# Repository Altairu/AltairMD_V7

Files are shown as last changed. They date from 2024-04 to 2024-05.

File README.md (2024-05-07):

# [**AltairMD_V7**](https://github.com/Altairu/AltairMD_V7)
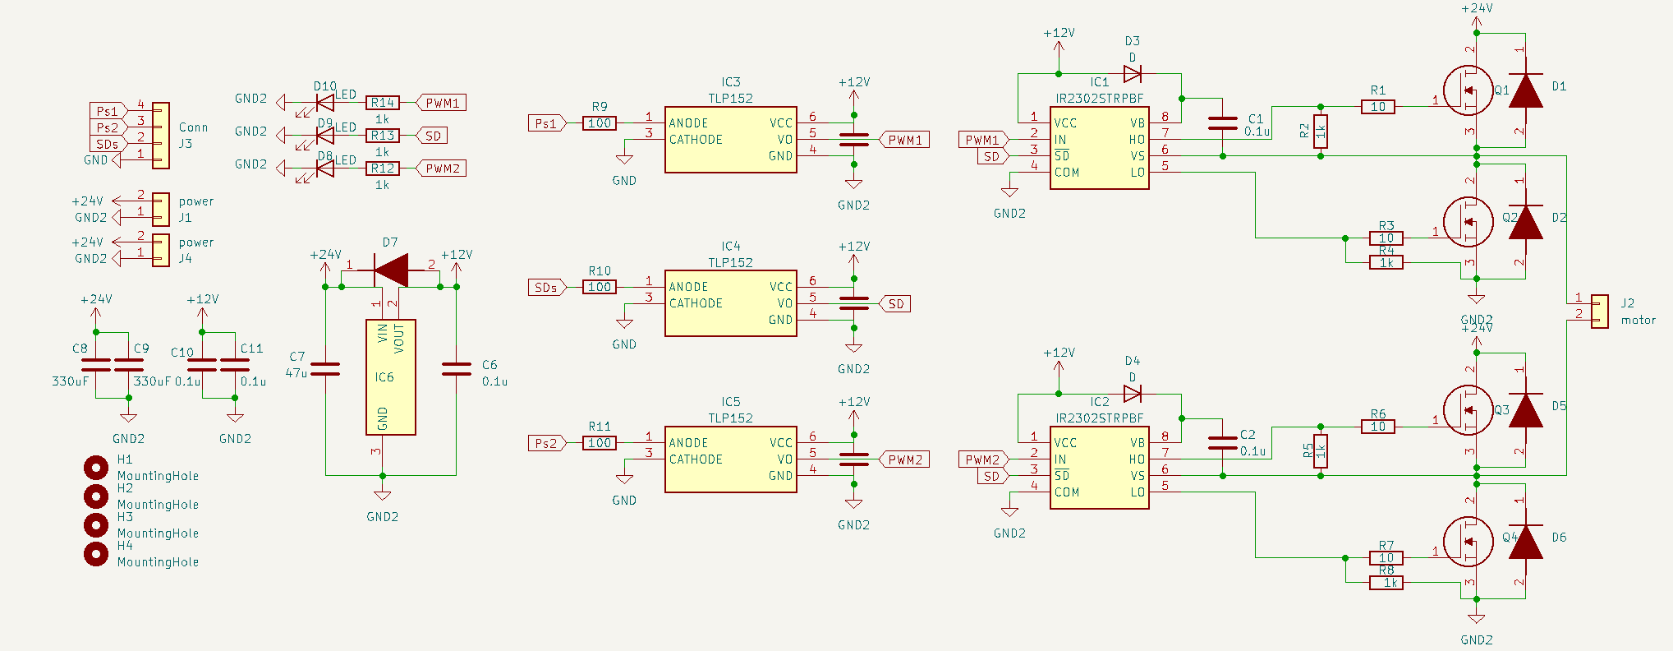
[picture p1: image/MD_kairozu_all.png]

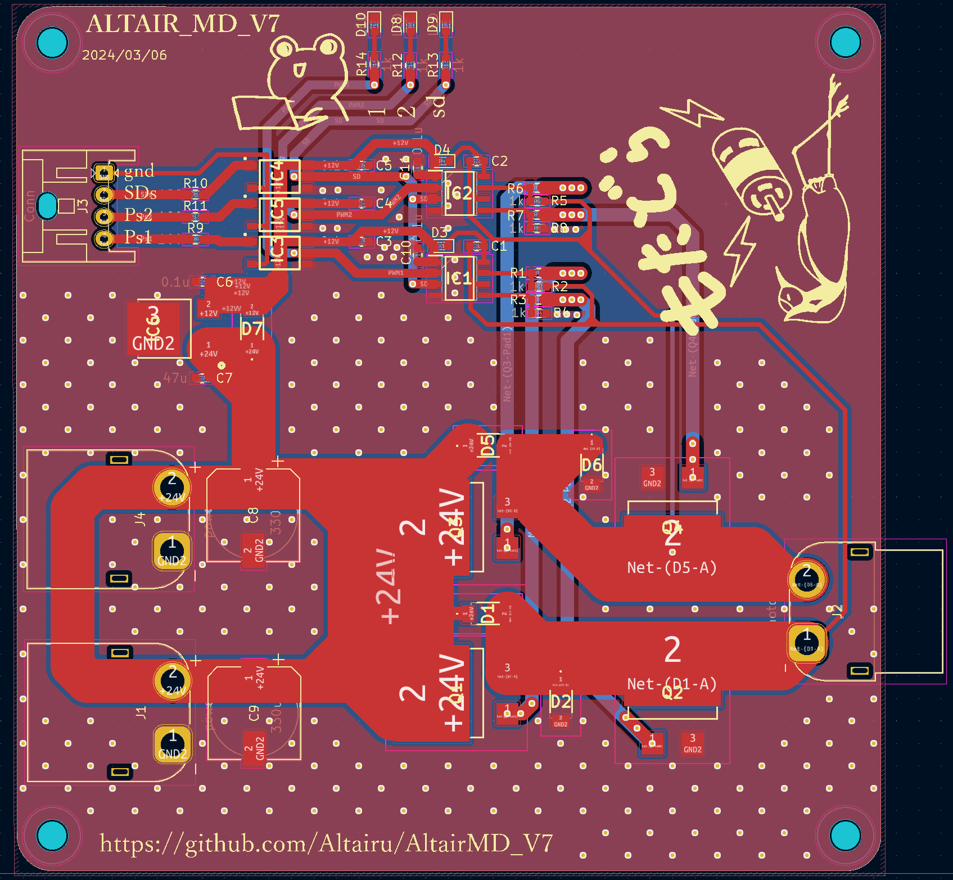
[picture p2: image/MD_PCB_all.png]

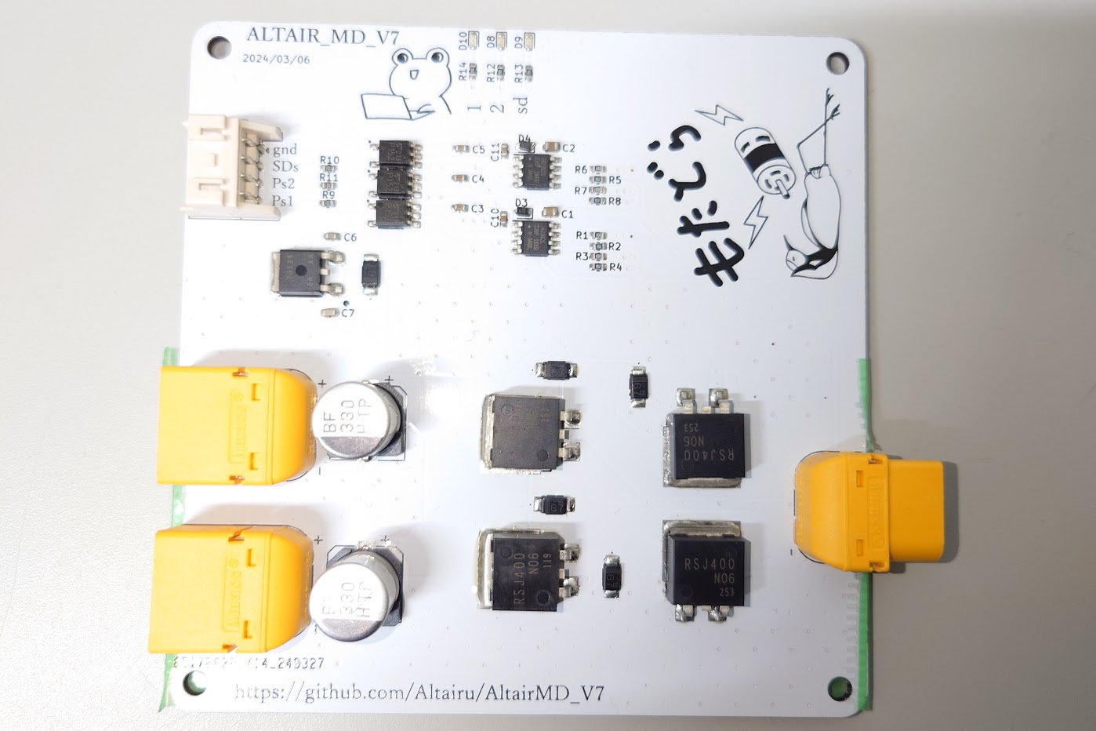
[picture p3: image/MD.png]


https://github.com/Altairu/AltairMD_V7
---
# **仕様**
* 30V~10V(フォトカプラを変更すると10V以下も可)
* 最大40A 

|SDs|Ps1|Ps2|出力|
|:----:|:----:|:----:|:----:|
|HIGH|LOW	|LOW	|停止|
|HIGH|LOW	|HIGH	|逆転|
|HIGH|HIGH	|LOW	|正転|
|HIGH|HIGH	|HIGH	|`ブレーキ`（非推奨）|
|LOW|X	|X	|0|

## **三端子レギュレーター** 
### **[NJM7812SDL1]()**
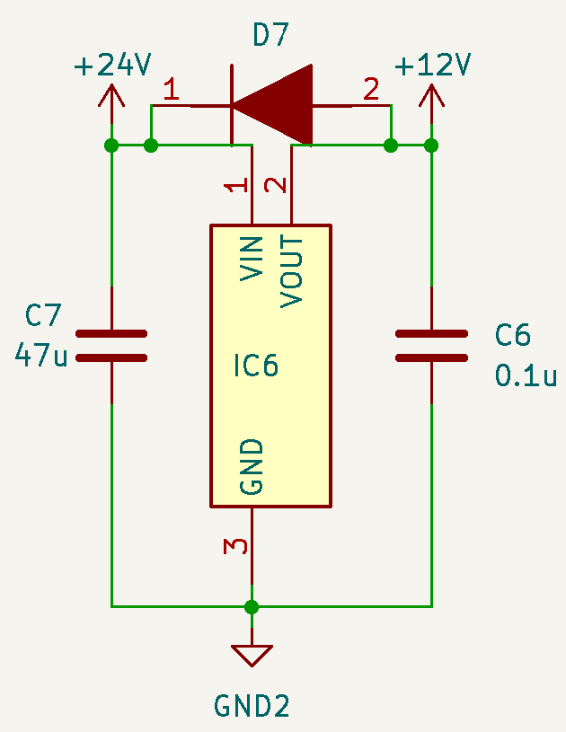
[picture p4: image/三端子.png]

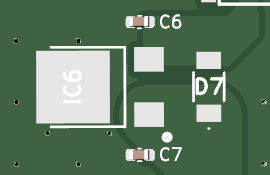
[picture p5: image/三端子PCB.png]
 

* **12Vに降圧**
* **端子が3つ(入力・グラウンド・出力）**
* **三端子レギュレータは落とした分の電圧をすべて`熱`として消費**
* **ダイオード**
レギュレータに逆電流が流れるのを防止
* **コンデンサ**
コンデンサは入力側と出力側に0.1～10[uF]程度入れるのが一般的

## **フォトカプラ**
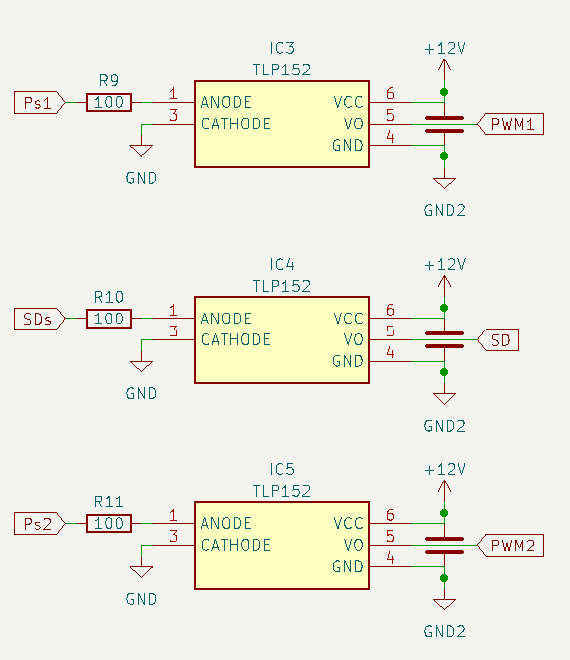
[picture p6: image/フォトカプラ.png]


### [TLP152](https://akizukidenshi.com/catalog/g/g110824/)
* 取り付け様式:	SMD/SMT	
* パッケージ/ケース:SOIC-6
* 電源電圧min.：10V
* 電源電圧max.：30V
* 出力電流：2A
* 入力電流max.：20mA
* 上昇応答時間：95ns
* 下降応答時間：110ns

## **MOSFET**
### [**RSJ400N10**](https://www.rohm.co.jp/products/mosfets/small-signal/single-nch/rsj400n10-product)

Nch 100V 40A Power MOSFET

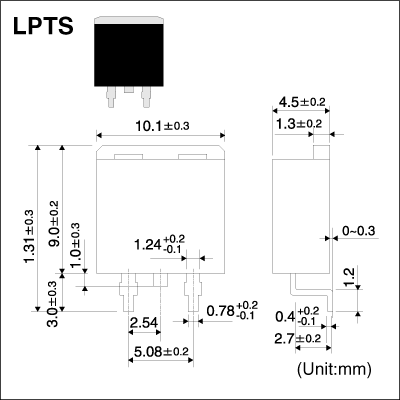
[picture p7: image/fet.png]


* 4V駆動タイプ
* Nチャンネル　パワーMOSFET
* 高速スイッチング
* 駆動回路が簡単
* 並列使用が容易

ゲート抵抗は10[Ω]で設定している

### **ハーフブリッジゲートドライバ**
### [**IR2302STRPBF**](https://akizukidenshi.com/catalog/g/g115656/)
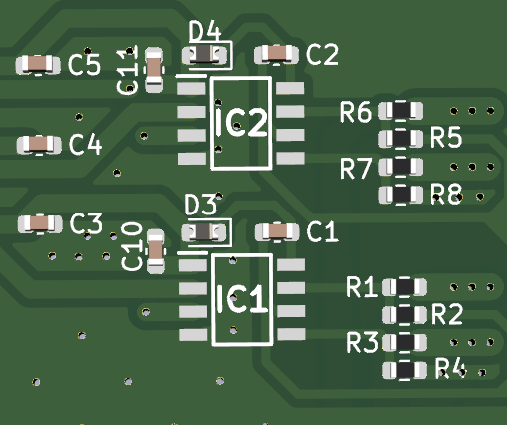
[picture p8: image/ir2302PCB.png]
 
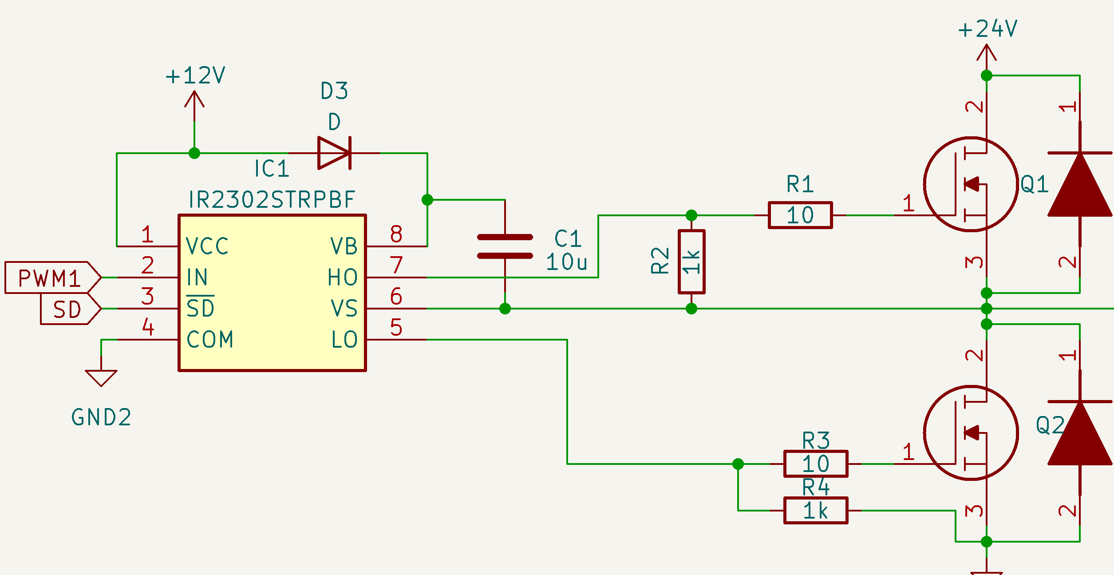
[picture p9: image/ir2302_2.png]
 
* IN端子
ハイサイドMOSFETをONにするか、ローサイドMOSFETをONにするかの切り替えを行う
Hが入力されるとハイサイド、Lが入力されるとローサイドがONとなる
**ハイサイドにNchMOSFETを使うためにブーストラップ回路を使用**
* ブートストラップコンデンサの容量は[10uF]
* ブートストラップダイオード
(ファストリカバリダイオード)
* `100％出力は不可`
ブートストラップ回路の制約で
コンデンサのチャージ時間が必要.

# Ｈブリッジ回路
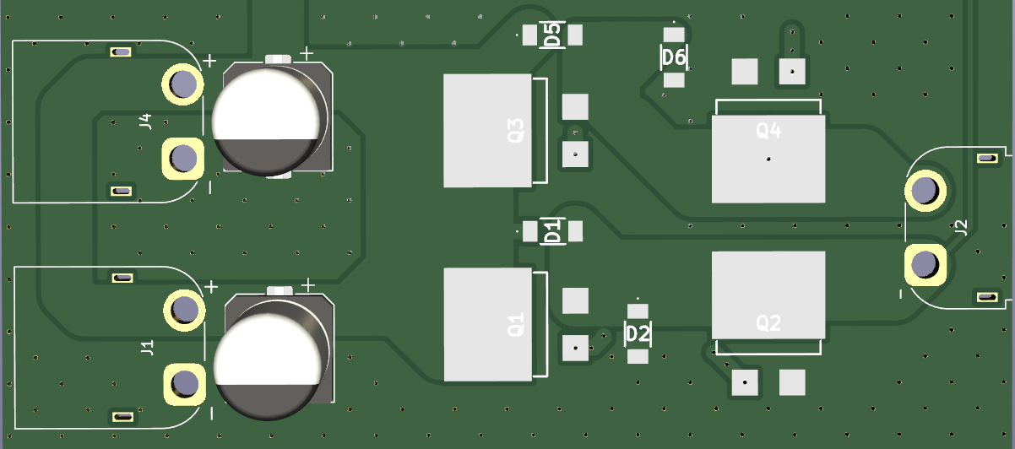
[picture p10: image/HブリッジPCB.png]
width:1000px
 

| Ps1 | Ps2 | Q1  | Q2  | Q3  | Q4  | 1 | 2 | 
| :----: | :----: | :----: | :----: | :----: | :----: | :----: | :----: |
| L | L | H | L | H | L | open | open | 
| L | H | H | H | L | L | L | H | 
| H | L | L | L | H | H | H | L | 
| H | H | H | H | H | H | L | L |

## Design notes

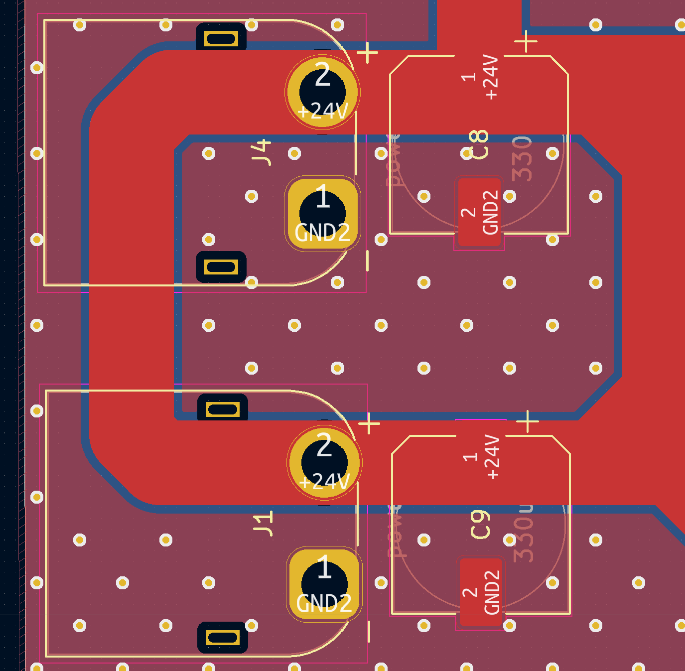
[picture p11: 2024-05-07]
image/バイパスコンPCB.png

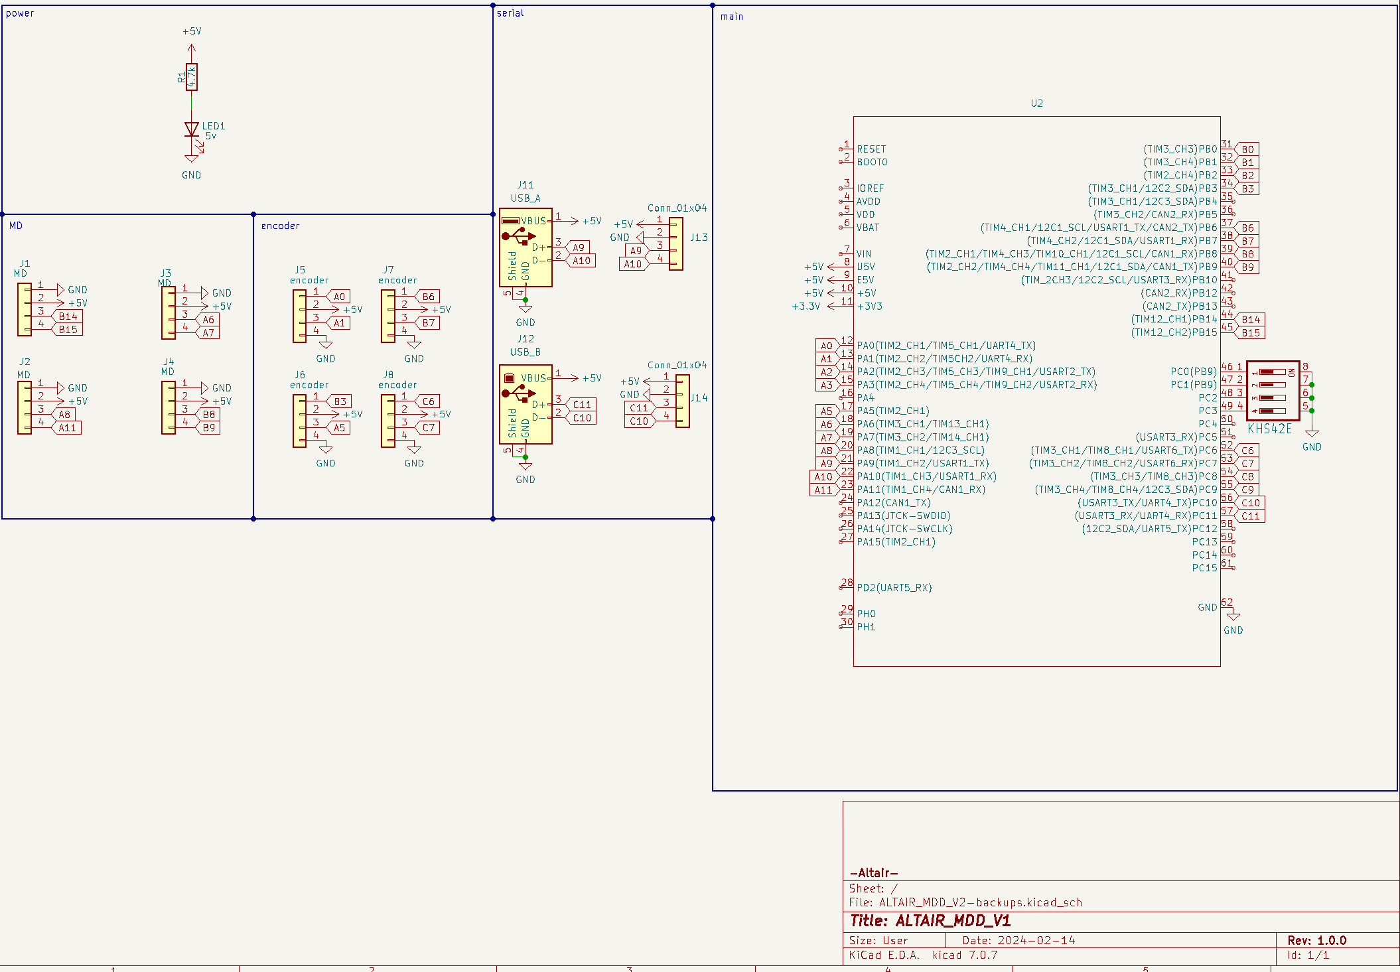
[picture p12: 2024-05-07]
image/MDD2.png

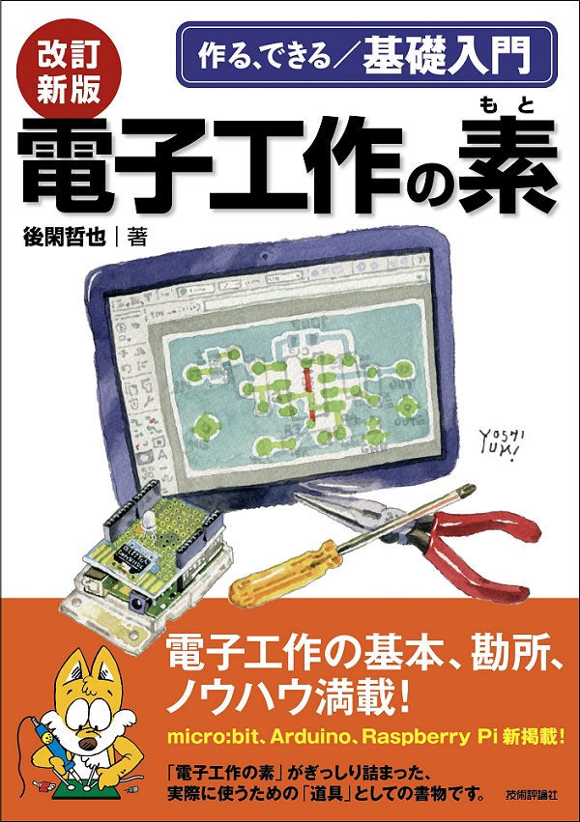
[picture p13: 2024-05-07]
image/kaironomoto.png

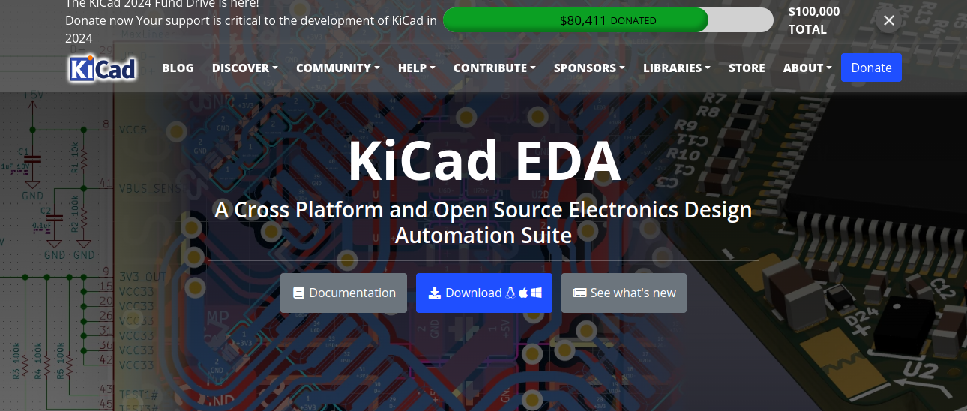
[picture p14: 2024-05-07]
image/kicad.png

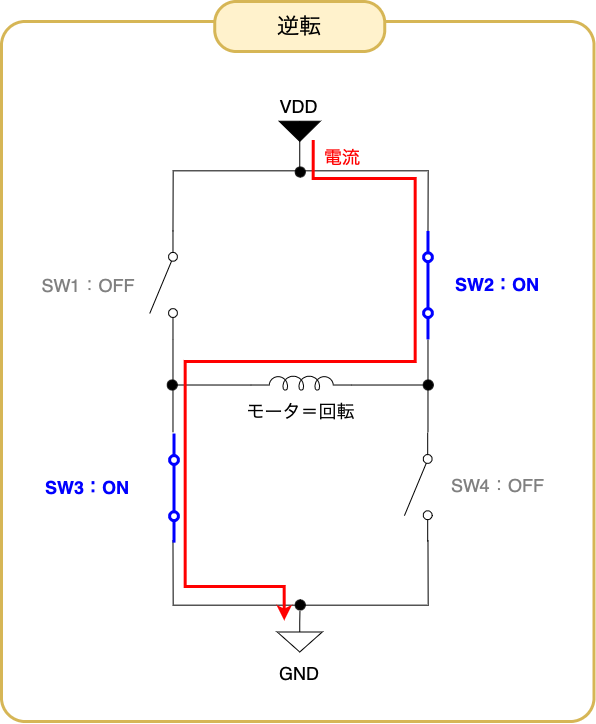
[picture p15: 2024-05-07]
image/1_files/165cf2e3f7085f0288b2cf0e68efcce5.png

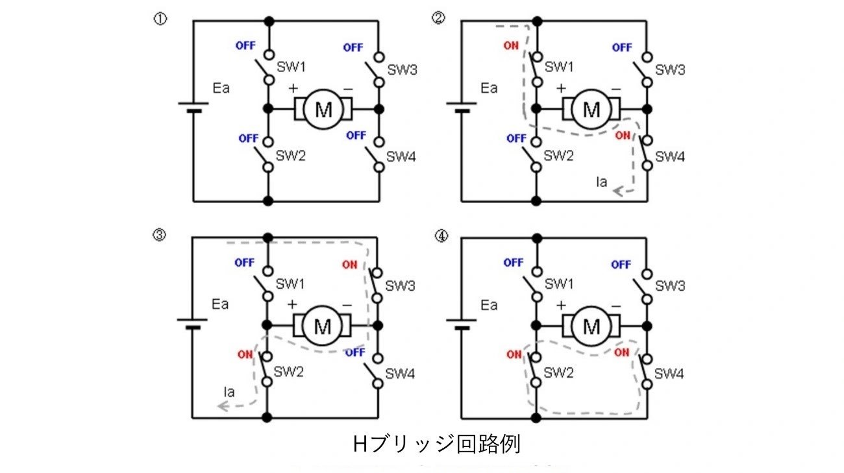
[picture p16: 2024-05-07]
image/Hブリッジ.png

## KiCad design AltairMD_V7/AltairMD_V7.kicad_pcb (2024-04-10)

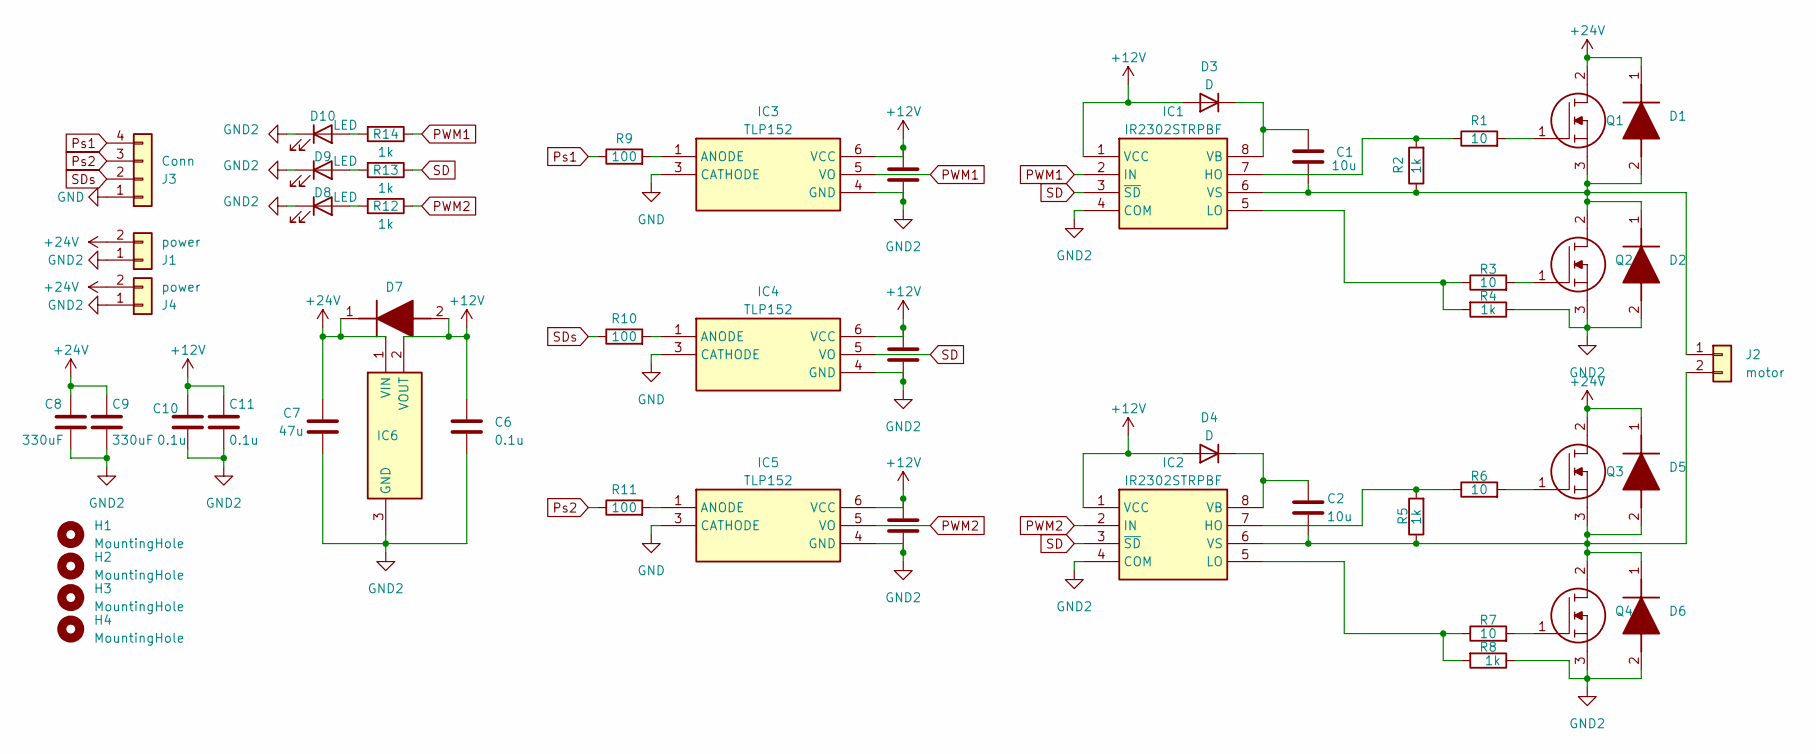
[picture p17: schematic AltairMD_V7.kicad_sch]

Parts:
C1, C2: 10u; C_0603_1608Metric
C3, C4, C5, C6, C10, C11: 0.1u; C_0603_1608Metric
C7: 47u; C_0603_1608Metric
C8, C9: 330uF; CP_Elec_10x10
D1, D2, D5, D6, D7: RF201LAM2STR; Manufacturer_Part_Number RF201LAM2STR
D3, D4: D; D_0603_1608Metric
D8, D9, D10: LED; LED_0603_1608Metric
H1, H2, H3, H4: MountingHole; MountingHole_3.2mm_M3
IC1, IC2: IR2302STRPBF; SOIC127P600X175-8N; Manufacturer_Part_Number IR2302STRPBF
IC3, IC4, IC5: TLP152; 11-4L1S_5-PIN-SOIC_; Manufacturer_Part_Number TLP152
IC6: NJM7800S-DL1; TO-252-3-L1; Manufacturer_Part_Number NJM7800S-DL1
J1, J4: power; AMASS_XT60PW-M_1x02_P7.20mm_Horizontal
J2: motor; AMASS_XT60PW-F_1x02_P7.20mm_Horizontal
J3: Conn; JST_XA_S04B-XASK-1_1x04_P2.50mm_Horizontal
Q1, Q2, Q3, Q4: RSJ400N06FRATL; R6024KNJTL; Manufacturer_Part_Number RSJ400N06FRATL
R1, R3, R6, R7: 10; R_0603_1608Metric
R2, R4, R5, R8, R12, R13, R14: 1k; R_0603_1608Metric
R9, R10, R11: 100; R_0603_1608Metric

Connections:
+12V: C3.1, C4.1, C5.1, C6.1, C10.1, C11.1, D3.2 (A), D4.2 (A), D7.2 (A), IC1.1 (VCC), IC2.1 (VCC), IC3.6 (VCC), IC4.6 (VCC), IC5.6 (VCC), IC6.2 (VOUT)
+24V: C7.1, C8.1, C9.1, D1.1 (K), D5.1 (K), D7.1 (K), IC6.1 (VIN), J1.2, J4.2, Q1.2, Q3.2
GND: IC3.3 (CATHODE), IC4.3 (CATHODE), IC5.3 (CATHODE), J3.1
GND2: C3.2, C4.2, C5.2, C6.2, C7.2, C8.2, C9.2, C10.2, C11.2, D2.2 (A), D6.2 (A), D8.1 (K), D9.1 (K), D10.1 (K), IC1.4 (COM), IC2.4 (COM), IC3.4 (GND), IC4.4 (GND), IC5.4 (GND), IC6.3 (GND), J1.1, J4.1, Q2.3, Q4.3, R4.1, R8.1
unnamed: C1.2, D1.2 (A), D2.1 (K), IC1.6 (VS), J2.1, Q1.3, Q2.2, R2.1
unnamed: C1.1, D3.1 (K), IC1.8 (VB)
unnamed: C2.1, D4.1 (K), IC2.8 (VB)
unnamed: C2.2, D5.2 (A), D6.1 (K), IC2.6 (VS), J2.2, Q3.3, Q4.2, R5.1
unnamed: D8.2 (A), R12.2
unnamed: D9.2 (A), R13.2
unnamed: D10.2 (A), R14.2
unnamed: IC1.7 (HO), R1.1, R2.2
unnamed: IC1.5 (LO), R3.1, R4.2
unnamed: IC2.7 (HO), R5.2, R6.1
unnamed: IC2.5 (LO), R7.1, R8.2
unnamed: IC3.1 (ANODE), R9.2
unnamed: IC4.1 (ANODE), R10.2
unnamed: IC5.1 (ANODE), R11.2
unnamed: Q1.1, R1.2
unnamed: Q2.1, R3.2
unnamed: Q3.1, R6.2
unnamed: Q4.1, R7.2
PWM1: IC1.2 (IN), IC3.5 (VO), R14.1
PWM2: IC2.2 (IN), IC5.5 (VO), R12.1
Ps1: J3.4, R9.1
Ps2: J3.3, R11.1
SD: IC1.3 (~SD), IC2.3 (~SD), IC4.5 (VO), R13.1
SDs: J3.2, R10.1

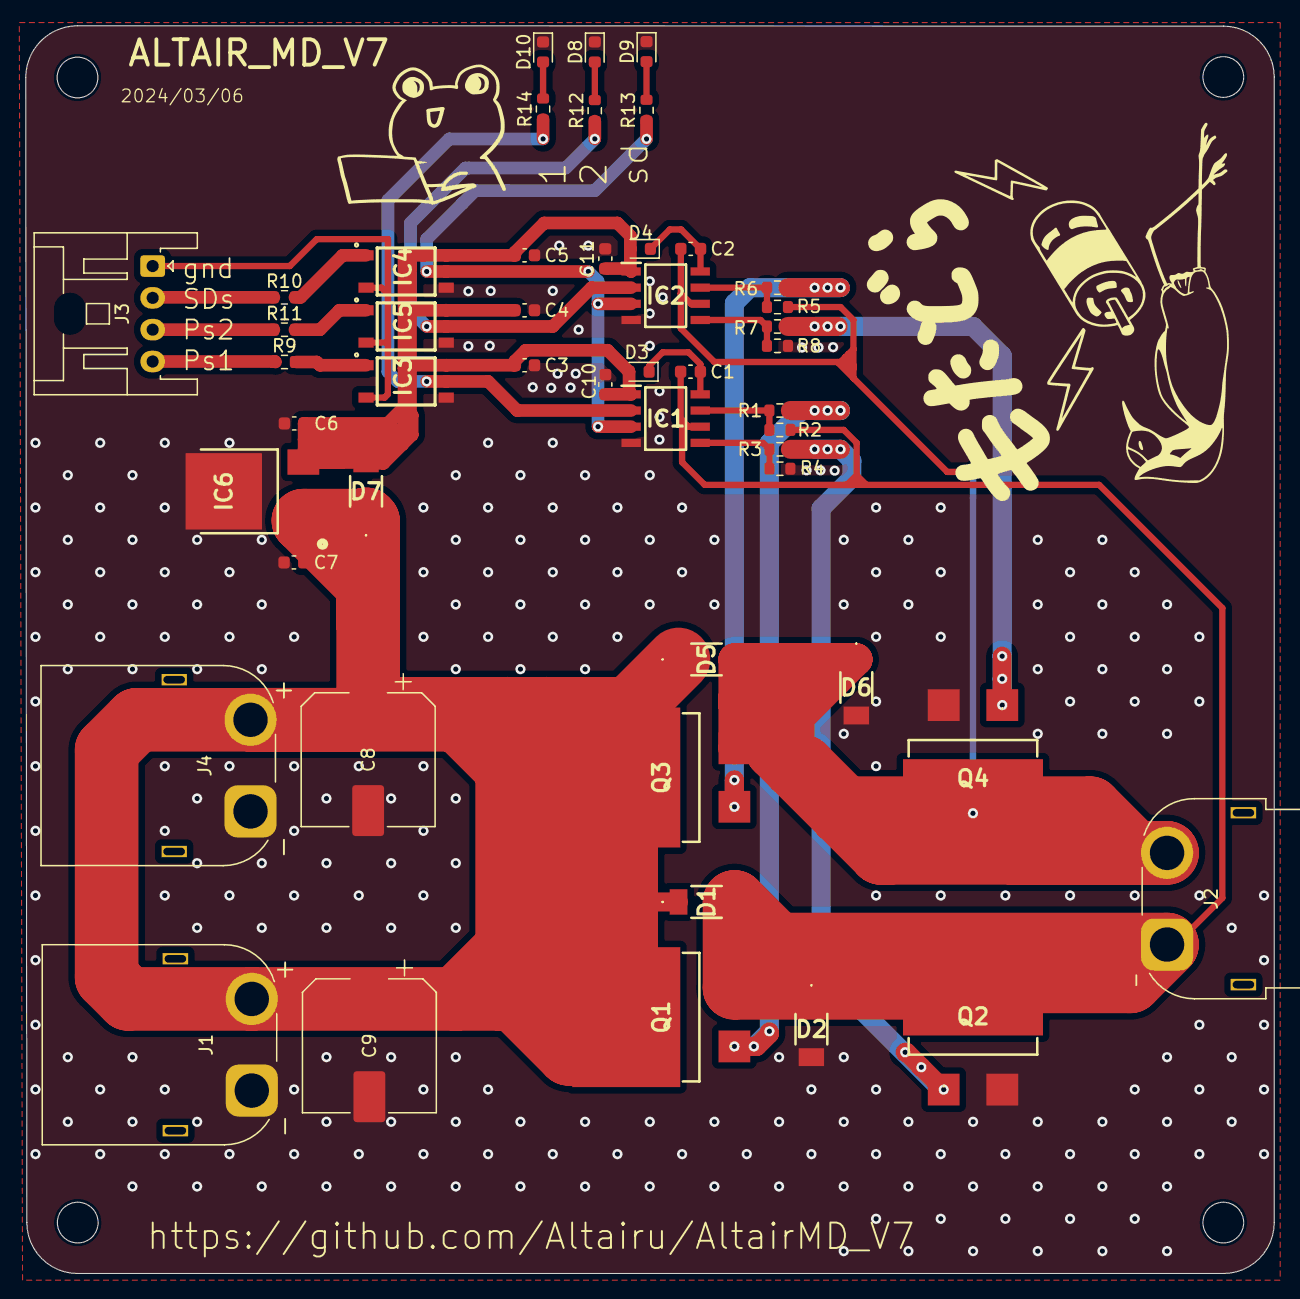
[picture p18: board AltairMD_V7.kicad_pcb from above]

Board: 2 copper layers, 98.1 x 98.0 mm, 53 parts (0 on the bottom side), 28 nets.
